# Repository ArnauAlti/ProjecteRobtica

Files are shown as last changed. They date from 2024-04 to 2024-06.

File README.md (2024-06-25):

# MiniGolfer
MiniGolfer es un robot el cual es capaz de jugar a minigolf.
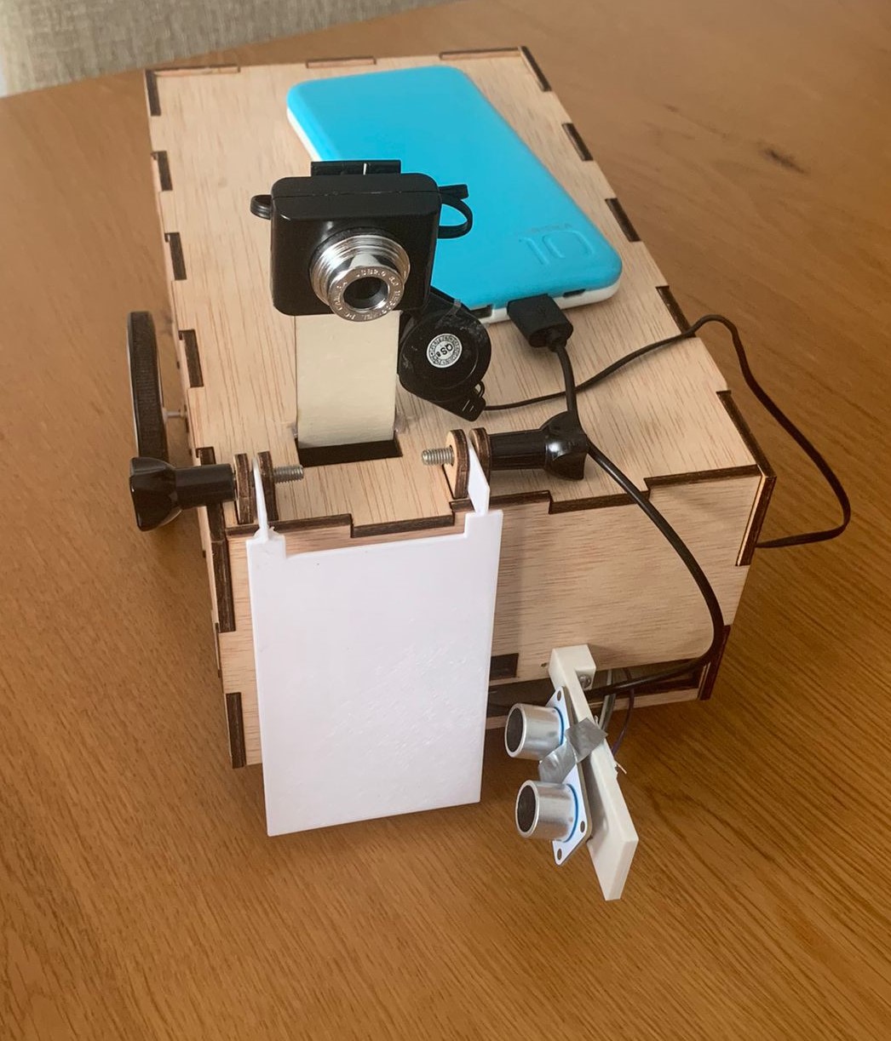
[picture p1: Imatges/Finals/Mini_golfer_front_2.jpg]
Mini_golfer


### [Contingut](#contingut)
### [Requeriments](#requeriments)
### [Components](#components)
### [Esquema HW](#esquema-hw)
### [Esquema SW](#esquema-sw)
### [Resultats Finals + Video](#resultats-finals--video)
### [Autors](#autors)

### Contingut

El robot està dissenyat per jugar al minigolf de manera autònoma. S’equipa amb dues rodes principals per al desplaçament i una roda addicional multidireccional per a una millor maniobrabilitat. El robot utilitza una càmera per localitzar i seguir la pilota de golf al camp de joc. Una vegada ha identificat la pilota, el robot s'aproxima a ella.
Per determinar la proximitat exacta a la pilota, el robot està equipat amb un sensor d'ultrasons. Quan el sensor detecta que la pilota està a l'abast, el robot s’atura. A continuació, activa un solenoide que mou una pala mecànica. Aquesta pala és responsable de colpejar la pilota, dirigir-la cap al forat.

### Requeriments
Les llibreries necessàries per aquest projecte son:
- RPi.GPIO
- OpenCV
- Numpy
- time

### Components
- Raspberry Pi 3 B+
- Cámara Raspberry
- 2 Motor Rodes
- Sensor de distancia por ultrasonidos
- Placa de prototipo
- Base para baterías (6xAA)
- Solenoide 5v
- Controlador de motores
- Bateria externa
- Relé

### Esquema HW
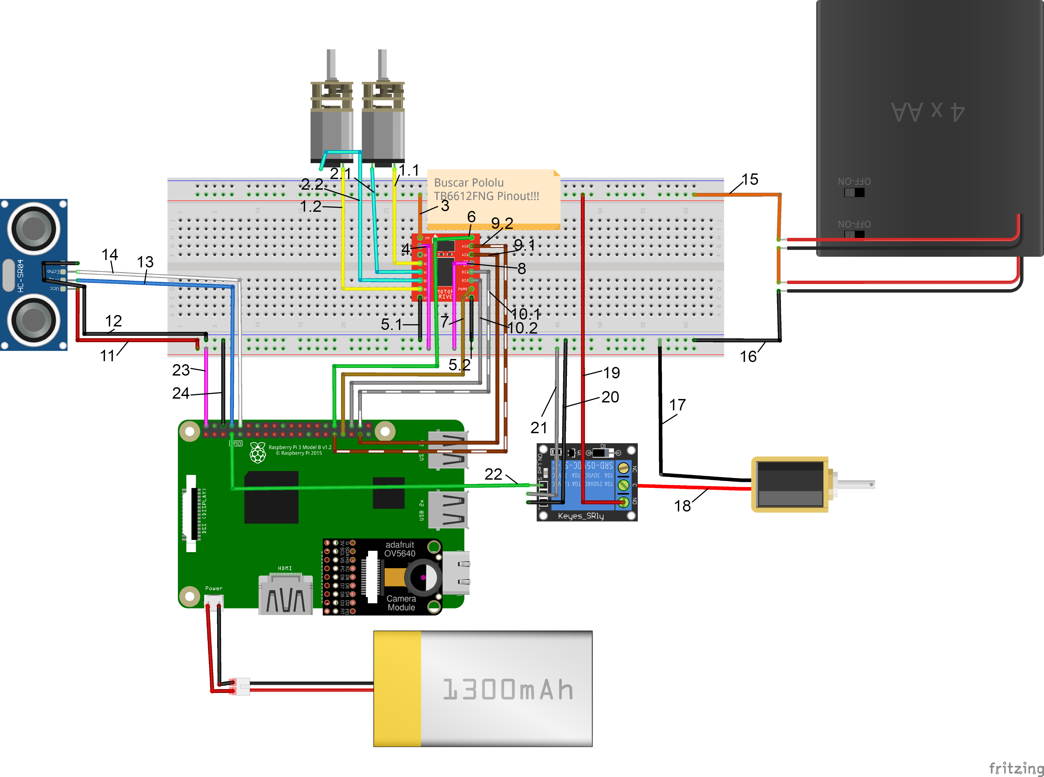
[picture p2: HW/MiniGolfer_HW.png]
MiniGolfer Hardware Diagram


1.1. Connexió positiu del motor A  
1.2. Connexió positiu del motor B  
2.1. Connexió negatiu del motor A  
2.2. Connexió negatiu del motor B  
3. Alimentació 9v  
4. 5V de Raspberry  
5.1. Connexió de terra del driver connectat al GND de Raspberry  
5.2. Connexió de terra del driver connectat al GND de Raspberry  
6. Senyal anàloga para el motor A connectat al GPIO 12 de Raspberry  
7. Senyal anàloga para el motor B connectat al GPIO 13 de Raspberry  
8. 5V de Raspberry  
9.1. Senyal d'entrada del motor A connectat al GPIO 26 de Raspberry  
9.2. Senyal d'entrada del motor A connectat al GPIO 6 de Raspberry  
10.1. Senyal d'entrada del motor B connectat al GPIO 20 de Raspberry  
10.2. Senyal d'entrada del motor B connectat al GPIO 16 de Raspberry  
11. Alimentació del sensor d'ultrasònics connectat al 5V de Raspberry  
12. Connexió de terra del sensor d'ultrasons connectat al GND de Raspberry  
13. Senyal trigger del sensor d'ultrasons connectat al GPIO 14 de Raspberry  
14. Senyal eco del sensor d'ultrasons connectat al GPIO 15 de Raspberry  
15. Positiu de la bateria  
16. GND de la bateria  
17. GND del solenoide  
18. Alimentació del solenoide  
19. Connexió alimentació del solenoide via relé  
20. GND del solenoide connectat de Raspberry  
21. VCC del Relé connectat de Raspberry  
22. Connexió de senyal de relé al GPIO 4 de Raspberry  
23. 5V de Raspberry al protoboard  
24. Connexió GND de Raspberry al protoboard  

Conexió extra USB: Càmera

### Esquema SW
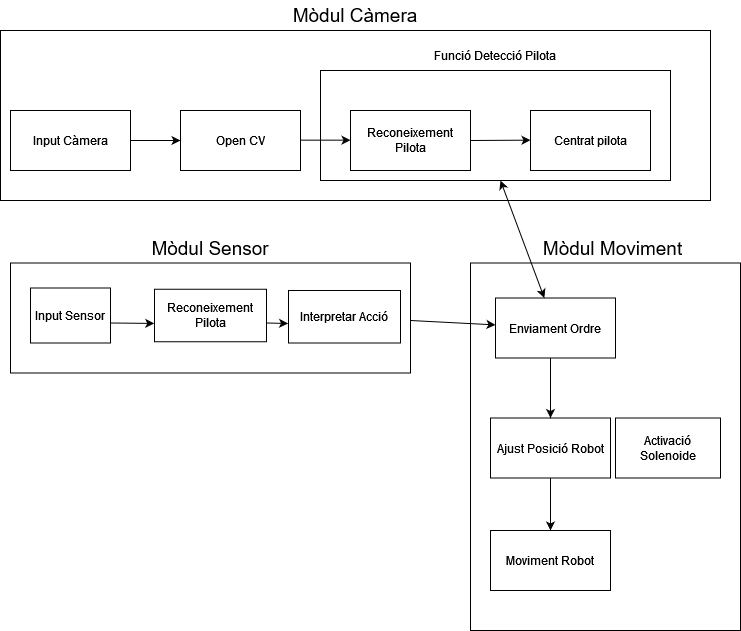
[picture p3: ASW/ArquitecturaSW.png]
Architecture MINIGOLFER


### Resultats Finals + Video
Miniatura del video (https://www.youtube.com/watch?v=eHLhcOQ6SlU)

### Autors

- Arnau Altimira Rubio
- Bernat Brustenga Garriga
- Wenpeng Ji
- Joaquim Calavera Madaula

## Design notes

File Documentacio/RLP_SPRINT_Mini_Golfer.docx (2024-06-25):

MiniGolfer

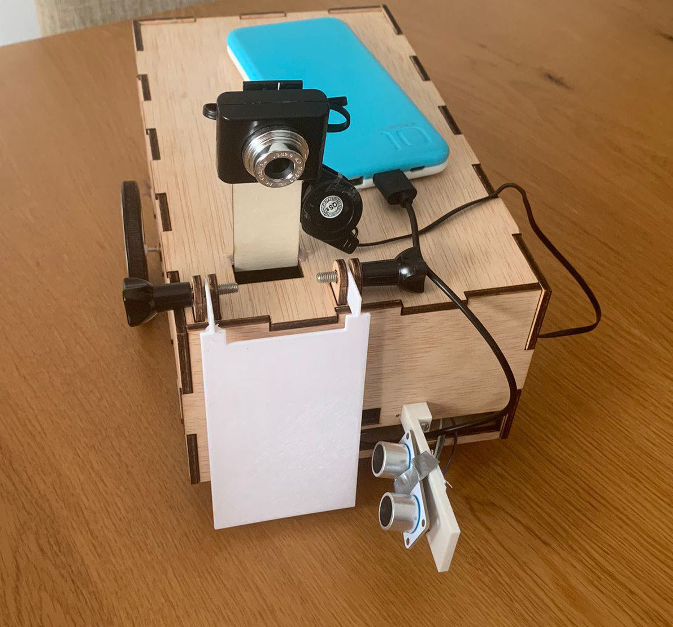
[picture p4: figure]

Arnau Altimira Rubio

Bernat Brustenga Garriga

Wenpeng Ji

Joaquim Calavera Madaula

Table of Contents

Project description 1

Electronic components 1

Scheme 2

Extra components and 3D pieces 4

Foreseen risks and contingency plan 6

MiniGolfer

Robot capaç de jugar al minigolf de forma autonoma

# Project description

El robot està dissenyat per jugar al minigolf de manera autònoma. S’equipa amb dues rodes principals per al desplaçament i una roda addicional multidireccional per a una millor maniobrabilitat. El robot utilitza una càmera per localitzar i seguir la pilota de golf al camp de joc. Una vegada ha identificat la pilota, el robot s'aproxima a ella cuidadosament.

Per determinar la proximitat exacta a la pilota, el robot està equipat amb un sensor d'ultrasons. Quan el sensor detecta que la pilota està a l'abast adequat, el robot s’atura. A continuació, activa un solenoide que mou una pala mecànica. Aquesta pala és responsable de colpejar la pilota, dirigir-la cap al forat.

# Electronic components

This is the list of the used components:

- Raspberry Pi 3 B+
- Càmera Raspberry
- Motor Rodes
- Sensor de distancia por ultrasons
- Placa de prototip
- Base para baterías (6xAA)
- Solenoide 5v
- Controlador de motors
- Bateria externa
- Relé

# Scheme

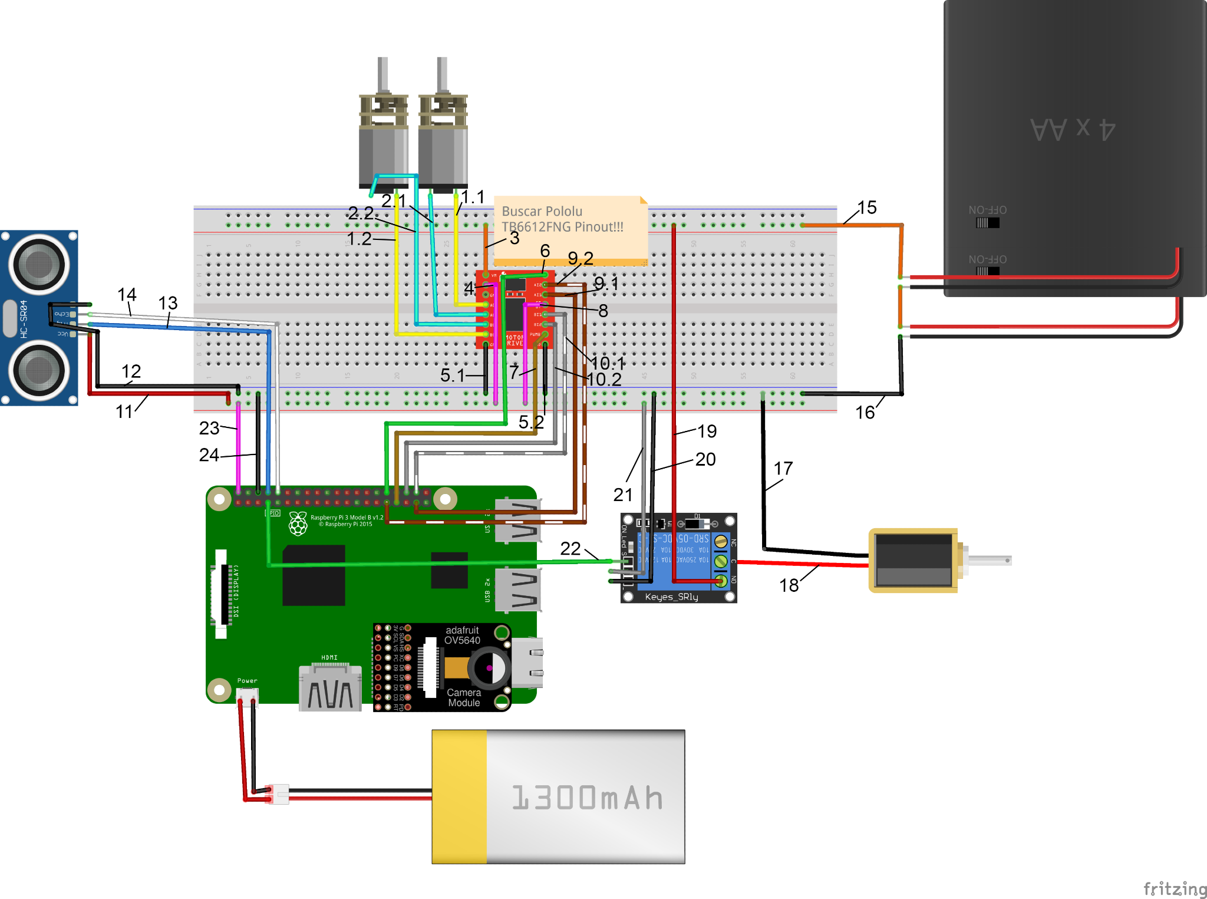
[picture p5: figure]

1.1. Connexió positiu del motor A

1.2. Connexió positiu del motor B

2.1. Connexió negatiu del motor A

2.2. Connexió negatiu del motor B

3. Alimentació 9v

4. 5V de Raspberry

5.1. Connexió de terra del driver connectat al GND de Raspberry

5.2. Connexió de terra del driver connectat al GND de Raspberry

6. Senyal anàloga para el motor A connectat al GPIO 12 de Raspberry

7. Senyal anàloga para el motor B connectat al GPIO 13 de Raspberry

8. 5V de Raspberry

9.1. Senyal d'entrada del motor A connectat al GPIO 26 de Raspberry

9.2. Senyal d'entrada del motor A connectat al GPIO 6 de Raspberry

10.1. Senyal d'entrada del motor B connectat al GPIO 20 de Raspberry

10.2. Senyal d'entrada del motor B connectat al GPIO 16 de Raspberry

11. Alimentació del sensor d'ultrasònics connectat al 5V de Raspberry

12. Connexió de terra del sensor d'ultrasons connectat al GND de Raspberry

13. Senyal trigger del sensor d'ultrasons connectat al GPIO 14 de Raspberry

14. Senyal eco del sensor d'ultrasons connectat al GPIO 15 de Raspberry

15. Positiu de la bateria

16. GND de la bateria

17. GND del solenoide

18. Alimentació del solenoide

19. Connexió alimentació del solenoide via relé

20. GND del solenoide connectat de Raspberry

21. VCC del Relé connectat de Raspberry

22. Connexió de senyal de relé al GPIO 4 de Raspberry

23. 5V de Raspberry al protoboard

24. Connexió GND de Raspberry al protoboard

Conexió extra USB: Càmera

Extra components and 3D pieces

- Caixa pel robot
- Suport per la càmera
- Fixador pel solenoide
- Paret per aguantar sensor de ultrasònics
- Suports per la pala x4
- Pala
- Caragol pala

Caixa pel robot: Caixa feta amb tall làser amb tapa extraïble, amb forats per fer les connexions amb la raspberry i per connectar les rodes, amb un forat extra per posar la molla del solenoide i empènyer la pala.

Suport per la càmera: Rectangle fet amb tall làser enganxat a la tapa de la caixa per deixar la càmera més elevada.

Fixador pel solenoide: Suport que aguanta el solenoide dins de la caixa perquè quan empenyi la pala no es mogui.

Paret per aguantar sensor d'ultrasònics: Enganxat davant del robot per col·locar un sensor d'ultrasònics apuntant davant de la pilota, aquest serveix perquè el robot pugui parar en el punt exacte perquè la pala estigui davant de la pilota.

Suports per la pala: Quatre suports enganxats a la tapa per posar la tapa mòbil.

Pala: Estructura que empenyerà el solenoide i donarà el cop a la pilota.

Caragol: Caragols per connectar la pala amb els suports de la pala per aconseguir el suport mòbil.

Fixador pel solenoide:

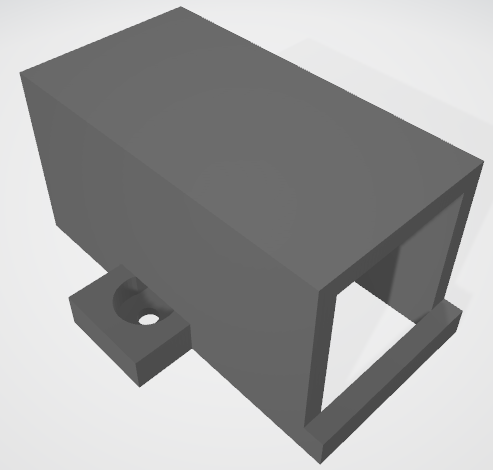
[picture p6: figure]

Paret per aguantar sensor de ultrasonidos:

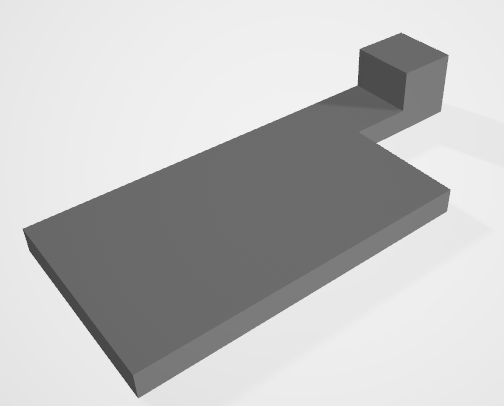
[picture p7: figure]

Suports per la pala x4:

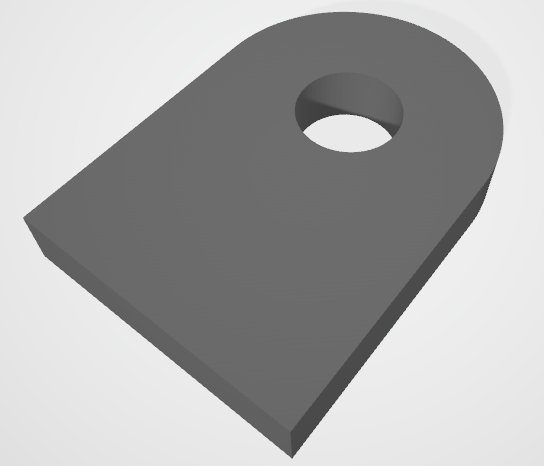
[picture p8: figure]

Pala:

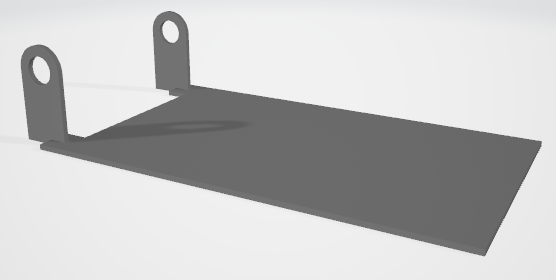
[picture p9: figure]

Caragol pala:

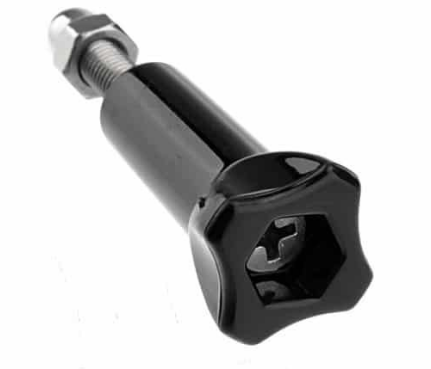
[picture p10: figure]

Risk # | Description | Probability (High/Medium/Low) | Impact (High/Medium/Low) | Contingency plan
Potència solenoide | El solenoide pot no tenir la suficient potència per empènyer la pilota a una certa distància. | Medium | Medium | Girar el solenoide, ja que hem trobat que té més potència quan comprimeix la molla que en l'etapa posterior.
Detecció càmera | No hi ha suficient camp de visió amb la càmera del projecte per trobar la pilota. | Medium | Low | No fa falta que la imatge de la càmera tingui la pilota en la imatge, el robot es pot moure fins a trobar la pilota.
Potencia motors de la roda | No tenir la suficient potencia per moure el robot | Low | High | Canviar a motors més potents o treure pes al robot.

References

This project has been inspired by the following Internet projects:

https://developer.nvidia.com/blog/jetson-project-of-the-month-this-autonomous-soccer-robot-can-point-shoot-and-score/

https://www.youtube.com/watch?v=jYL_Gjumi4I (Construir Robot Minigolf lego)

RPL - Computer Engineering. UAB (Barcelona) 2023-2024

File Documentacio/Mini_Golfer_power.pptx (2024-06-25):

## MiniGolfer


Un robot capaç de jugar al minigolf de forma autónoma

Arnau Altimira Rubio
Bernat Brustenga Garriga
Wenpeng Ji
Joaquim Calavera Madaula

ROBÒTICA, LLENGUATGE I PLANIFICACIÓ – ENGINYERIA INFORMÀTICA - UAB

## 1.Arquitectura hardware

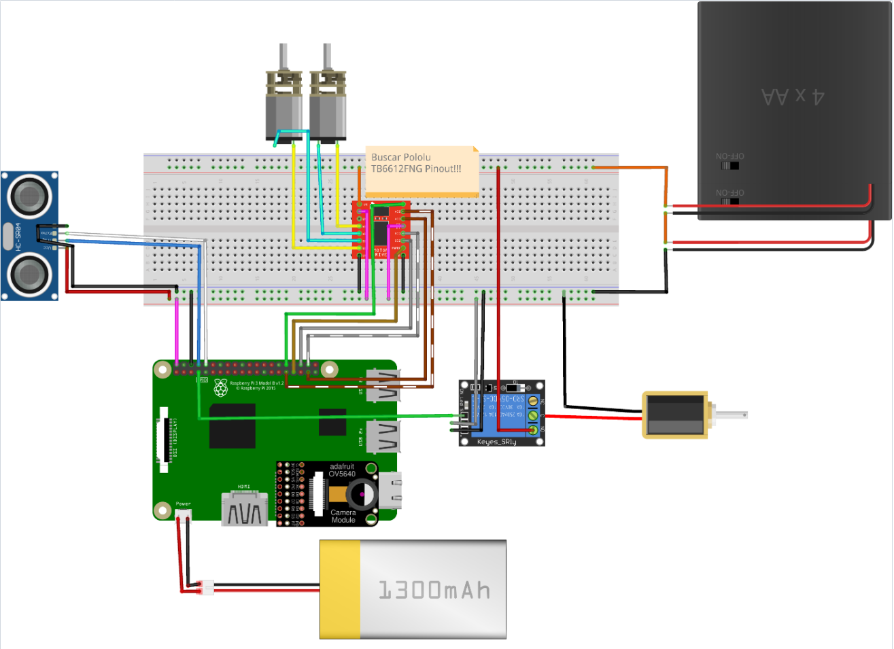
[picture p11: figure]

## 2.Arquitectura software


## 3. Algorísmica

- 1-Moviment rotatori -> Buscar Pilota
- 2-Pilota trobada -> Centrar la pilota amb la pala
- 3-Aproximació a la pilota -> sensor detecta pilota prop de la pala
- 4-Activació del solenoide per a golpejar la pilota

## Fotos, Video i Git

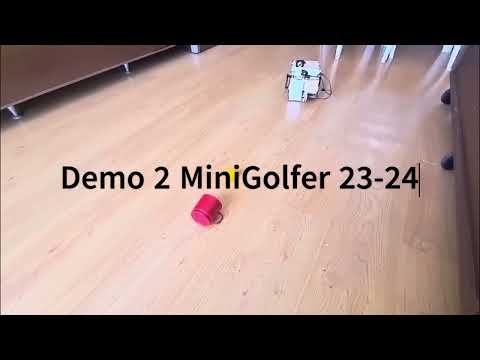
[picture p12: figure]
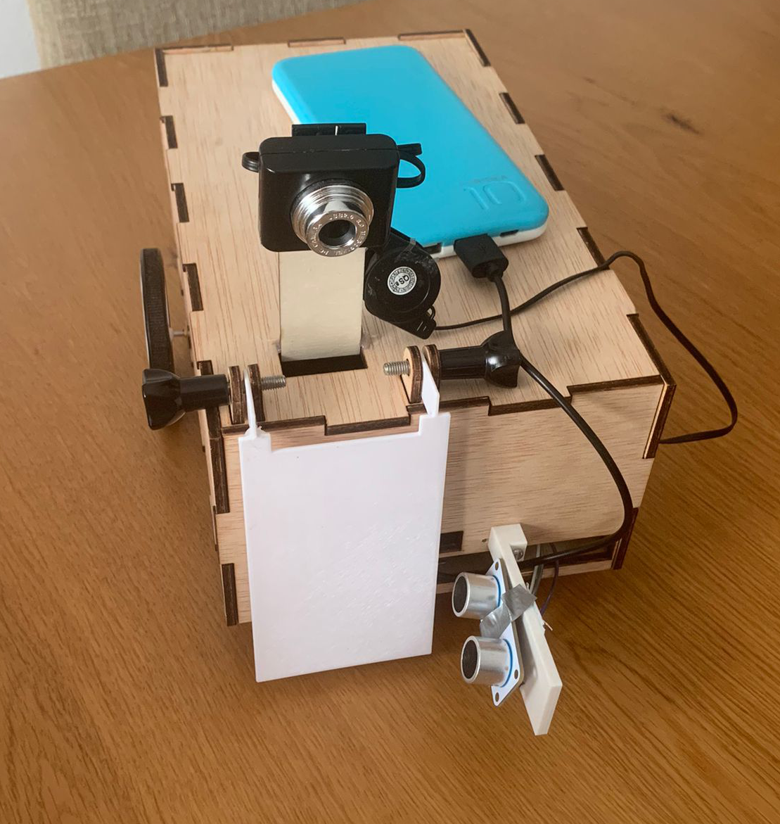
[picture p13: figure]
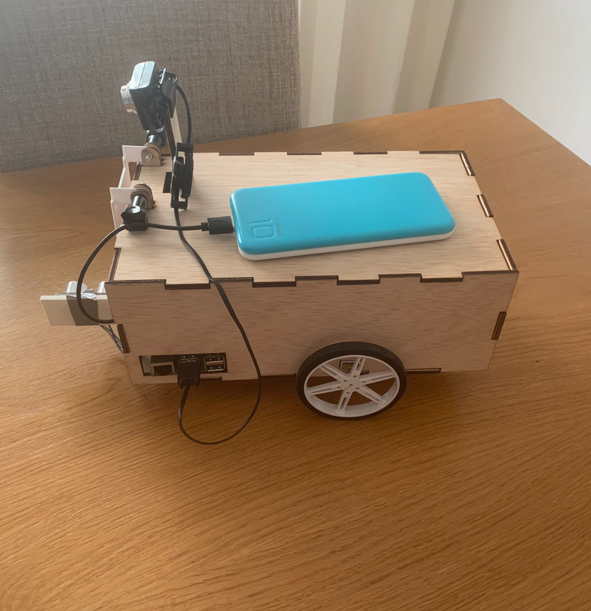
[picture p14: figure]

https://github.com/ArnauAlti/ProjecteRobtica/tree/main

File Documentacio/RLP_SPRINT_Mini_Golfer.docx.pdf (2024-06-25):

RPL - Computer Engineering. UAB (Barcelona) 2023-2024

# MiniGolfer

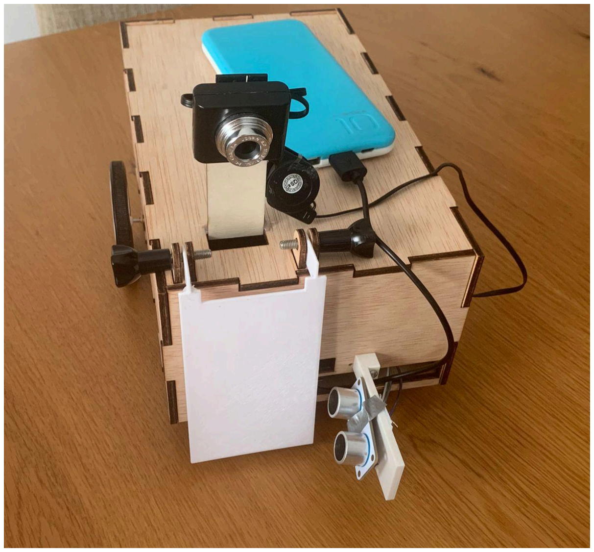
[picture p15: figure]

Arnau Altimira Rubio

Bernat Brustenga Garriga

Wenpeng Ji

Joaquim Calavera Madaula

# Table of Contents

ROBOT_NAME

# MiniGolfer

Robot capaç de jugar al minigolf de forma autonoma

Project description

El robot està dissenyat per jugar al minigolf de manera autònoma. S’equipa amb dues rodes principals per al desplaçament i una roda addicional multidireccional per a una millor maniobrabilitat. El robot utilitza una càmera per localitzar i seguir la pilota de golf al camp de joc. Una vegada ha identificat la pilota, el robot s'aproxima a ella cuidadosament.

Per determinar la proximitat exacta a la pilota, el robot està equipat amb un sensor d'ultrasons. Quan el sensor detecta que la pilota està a l'abast adequat, el robot s’atura. A continuació, activa un solenoide que mou una pala mecànica. Aquesta pala és responsable de colpejar la pilota, dirigir-la cap al forat.

Electronic components
This is the list of the used components:

■ Raspberry Pi 3 B+
■ Càmera Raspberry
■ Motor Rodes
■ Sensor de distancia por ultrasons ■ Placa de prototip
■ Base para baterías (6xAA)
■ Solenoide 5v
■ Controlador de motors
■ Bateria externa
■ Relé
ROBOT_NAME | 1

Scheme

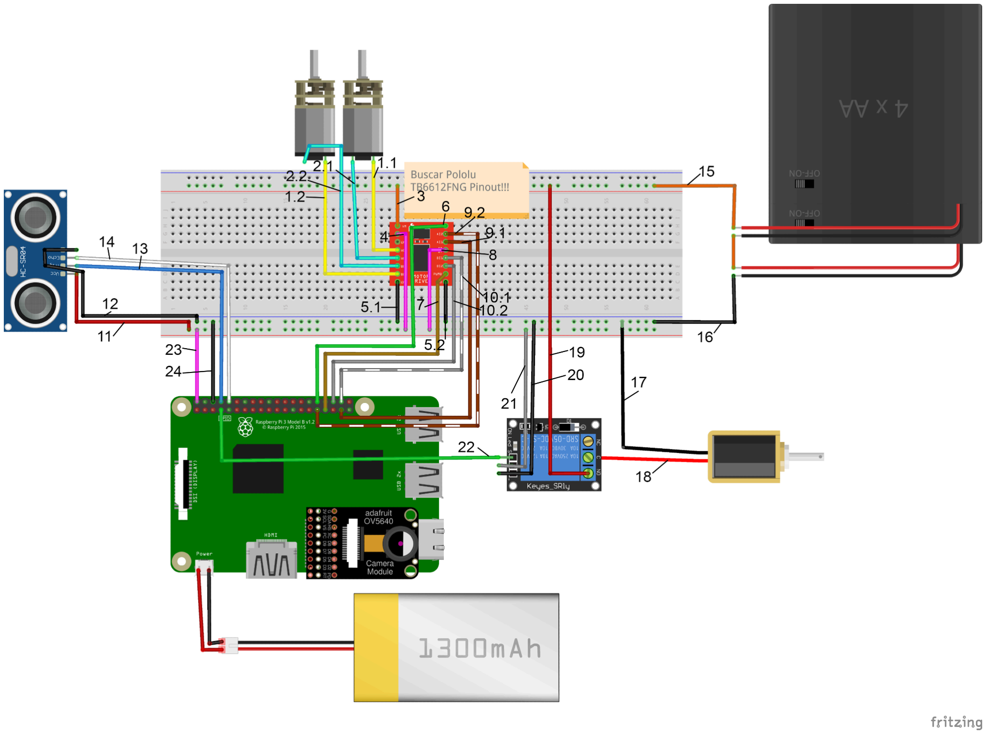
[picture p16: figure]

MiniGolfer | 2

### 1.1. Connexió positiu del motor A 1.2. Connexió positiu del motor B 2.1. Connexió negatiu del motor A 2.2. Connexió negatiu del motor B 3. Alimentació 9v

4. 5V de Raspberry

### 5.1. Connexió de terra del driver connectat al GND de Raspberry 5.2. Connexió de terra del driver connectat al GND de Raspberry 6. Senyal anàloga para el motor A connectat al GPIO 12 de Raspberry 7. Senyal anàloga para el motor B connectat al GPIO 13 de Raspberry

8. 5V de Raspberry

9.1. Senyal d'entrada del motor A connectat al GPIO 26 de Raspberry 9.2. Senyal d'entrada del motor A connectat al GPIO 6 de Raspberry 10.1. Senyal d'entrada del motor B connectat al GPIO 20 de Raspberry 10.2. Senyal d'entrada del motor B connectat al GPIO 16 de Raspberry 11. Alimentació del sensor d'ultrasònics connectat al 5V de Raspberry 12. Connexió de terra del sensor d'ultrasons connectat al GND de Raspberry 13. Senyal trigger del sensor d'ultrasons connectat al GPIO 14 de Raspberry 14. Senyal eco del sensor d'ultrasons connectat al GPIO 15 de Raspberry 15. Positiu de la bateria 16. GND de la bateria 17. GND del solenoide 18. Alimentació del solenoide 19. Connexió alimentació del solenoide via relé 20. GND del solenoide connectat de Raspberry 21. VCC del Relé connectat de Raspberry 22. Connexió de senyal de relé al GPIO 4 de Raspberry
23. 5V de Raspberry al protoboard

### 24. Connexió GND de Raspberry al protoboard

Conexió extra USB: Càmera

MiniGolfer | 3

Extra components and 3D pieces

■ Caixa pel robot

■ Suport per la càmera

■ Fixador pel solenoide

■ Paret per aguantar sensor de ultrasònics

■ Suports per la pala x4

■ Pala

■ Caragol pala

Caixa pel robot: Caixa feta amb tall làser amb tapa extraïble, amb forats per fer les connexions amb la raspberry i per connectar les rodes, amb un forat extra per posar la molla del solenoide i empènyer la pala.

Suport per la càmera: Rectangle fet amb tall làser enganxat a la tapa de la caixa per deixar la càmera més elevada.

Fixador pel solenoide: Suport que aguanta el solenoide dins de la caixa perquè quan empenyi la pala no es mogui.

Paret per aguantar sensor d'ultrasònics: Enganxat davant del robot per col·locar un sensor d'ultrasònics apuntant davant de la pilota, aquest serveix perquè el robot pugui parar en el punt exacte perquè la pala estigui davant de la pilota.

Suports per la pala: Quatre suports enganxats a la tapa per posar la tapa mòbil.

Pala: Estructura que empenyerà el solenoide i donarà el cop a la pilota.

Caragol: Caragols per connectar la pala amb els suports de la pala per aconseguir el suport mòbil.

MiniGolfer | 4

Fixador pel solenoide:

Paret per aguantar sensor de ultrasonidos:

Suports per la pala x4:

Pala:


Caragol pala:

MiniGolfer | 5

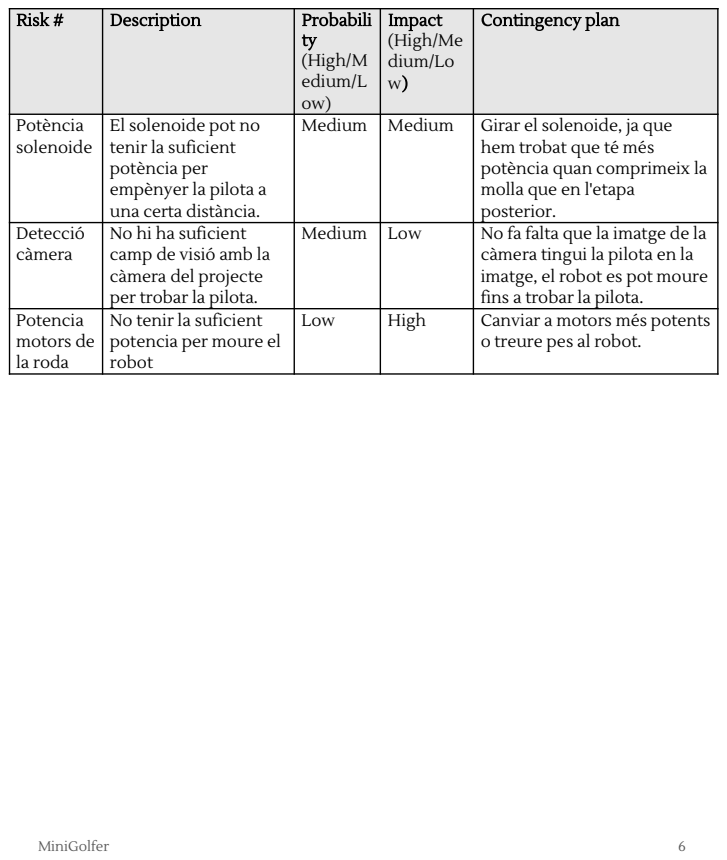
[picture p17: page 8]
MiniGolfer

Risk # | Description | Probabili ty (High/M edium/L ow) | Impact (High/Me dium/Lo w) | Contingency plan

Potència solenoide | El solenoide pot no tenir la suficient potència per empènyer la pilota a una certa distància. | Medium | Medium | Girar el solenoide, ja que hem trobat que té més potència quan comprimeix la molla que en l'etapa posterior.

Detecció càmera | No hi ha suficient camp de visió amb la càmera del projecte per trobar la pilota. | Medium | Low | No fa falta que la imatge de la càmera tingui la pilota en la imatge, el robot es pot moure fins a trobar la pilota.

Potencia motors de la roda | No tenir la suficient potencia per moure el robot | Low | High | Canviar a motors més potents o treure pes al robot.

# References

This project has been inspired by the following Internet projects:

https://developer.nvidia.com/blog/jetson-project-of-the-month-this-autonomous-soccer-robot-can-point-shoot-and-score/

https://www.youtube.com/watch?v=jYL_Gjumi4I (Construir Robot Minigolf lego)

MiniGolfer | 7

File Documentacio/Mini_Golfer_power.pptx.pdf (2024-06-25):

# MiniGolfer

Arnau Altimira Rubio

Bernat Brustenga Garriga

Wenpeng Ji

Joaquim Calavera Madaula

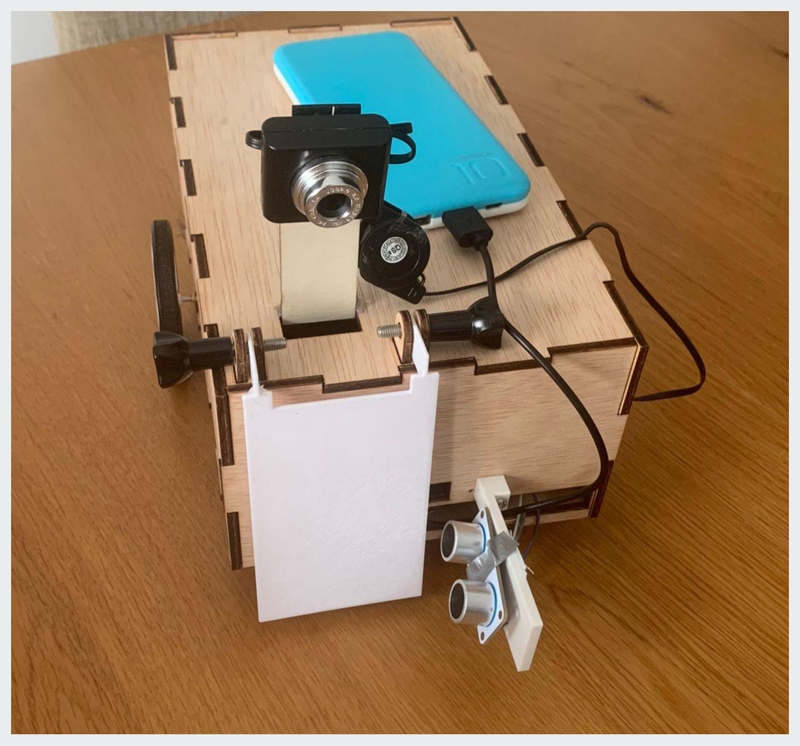
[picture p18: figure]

Un robot capaç de jugar al minigolf de forma autónoma

ROBÒTICA, LLENGUATGE I PLANIFICACIÓ – ENGINYERIA INFORMÀTICA - UAB

# 1.Arquitectura hardware

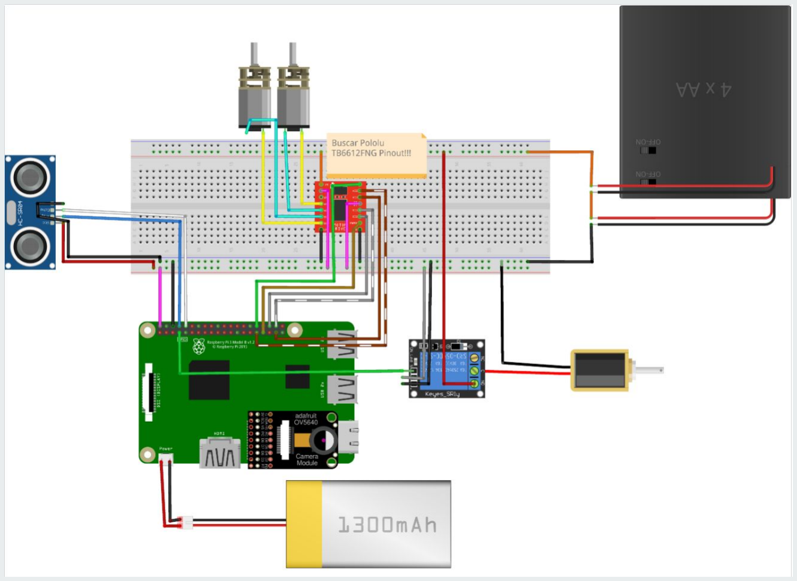
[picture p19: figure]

# 2.Arquitectura software

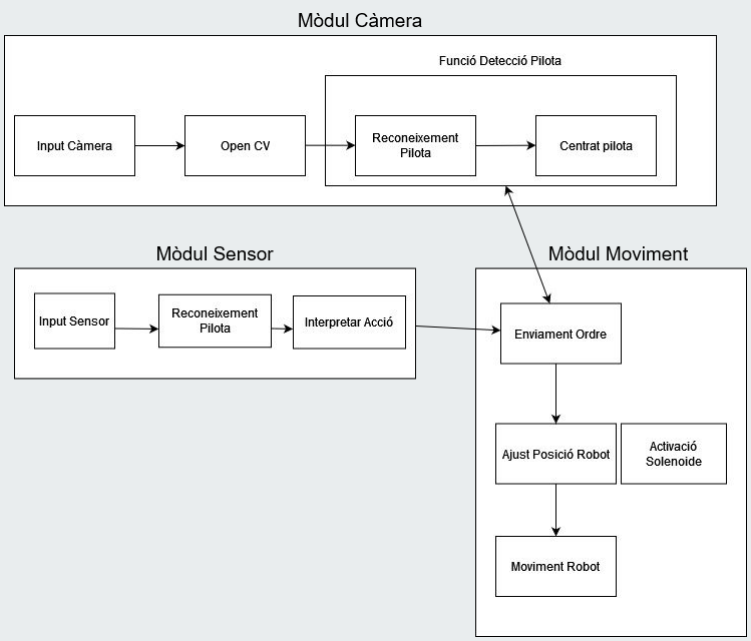
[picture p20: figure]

# 3. Algorísmica

1-Moviment rotatori -> Buscar Pilota

2-Pilota trobada -> Centrar la pilota amb la pala

3-Aproximació a la pilota -> sensor detecta pilota prop de la pala

4-Activació del solenoide per a golpejar la pilota

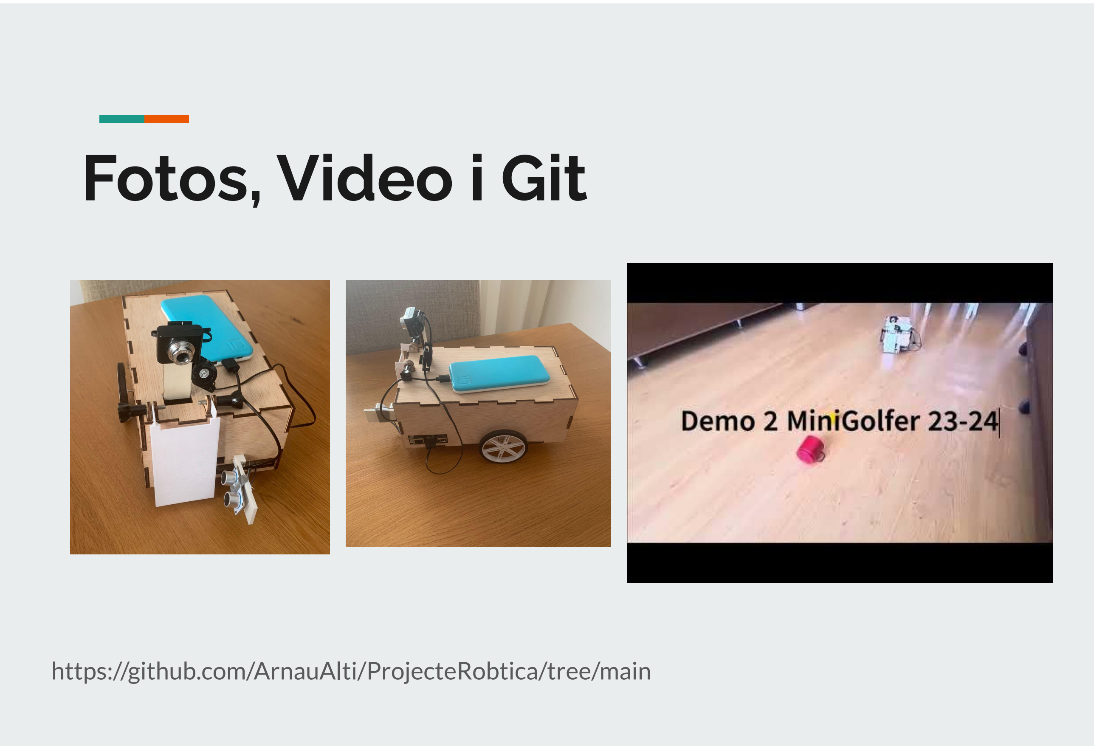
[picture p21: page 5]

# Fotos, Video i Git

https://github.com/ArnauAlti/ProjecteRobtica/tree/main

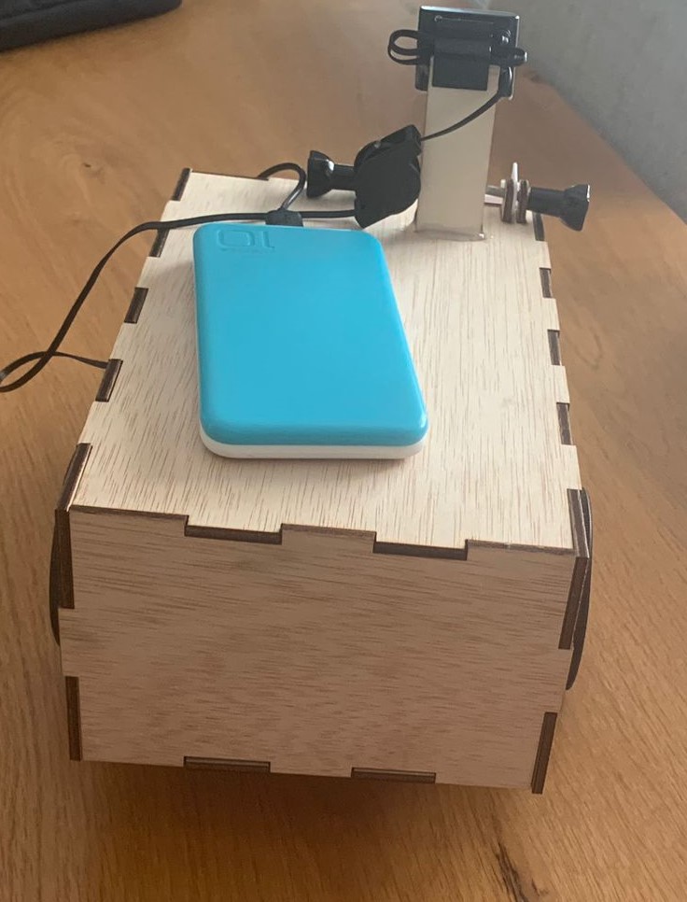
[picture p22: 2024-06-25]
Imatges/Finals/Mini_golfer_back.jpg

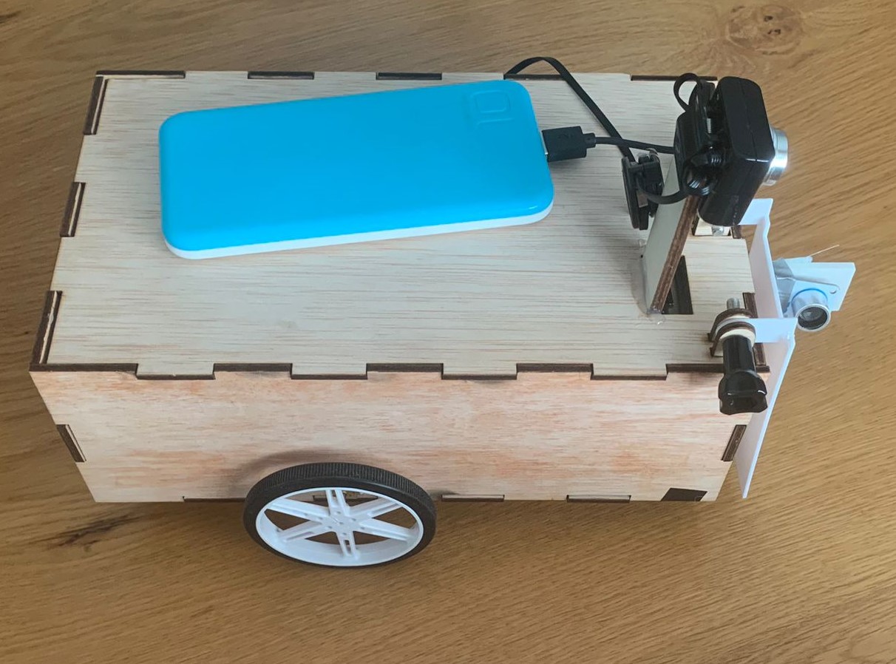
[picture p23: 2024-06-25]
Imatges/Finals/Mini_golfer_left.jpg

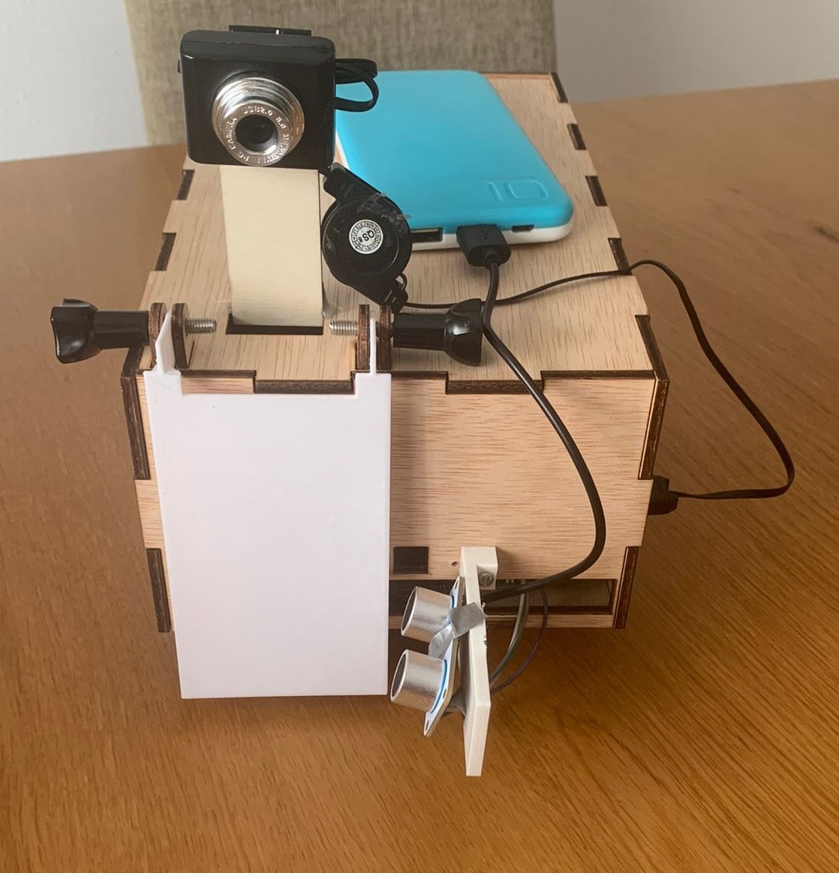
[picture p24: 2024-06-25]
Imatges/Finals/Mini_golfer_front.jpg

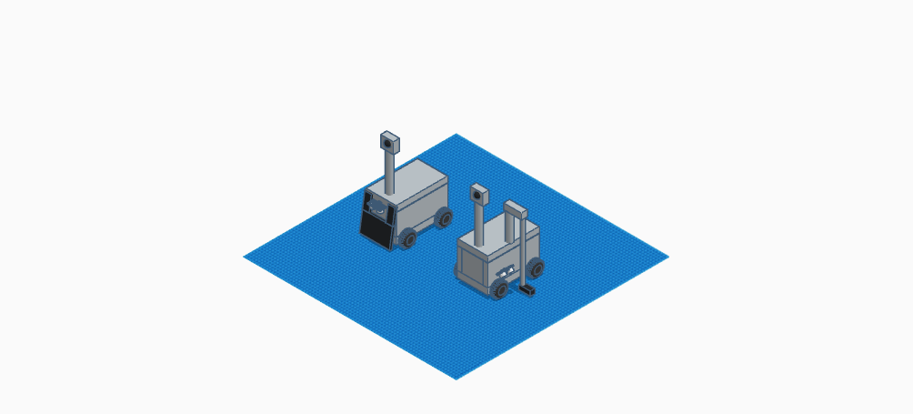
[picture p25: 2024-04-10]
Imatges/Previes/Minigolf_Model_1.png

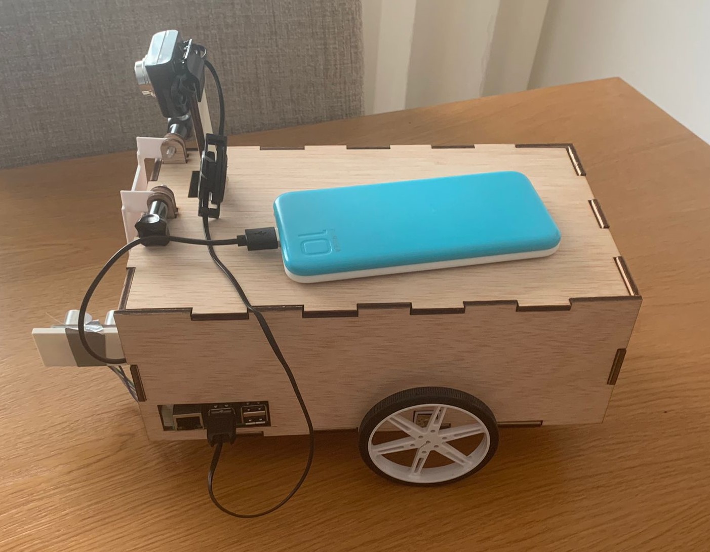
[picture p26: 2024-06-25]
Imatges/Finals/Mini_golfer_right.jpg

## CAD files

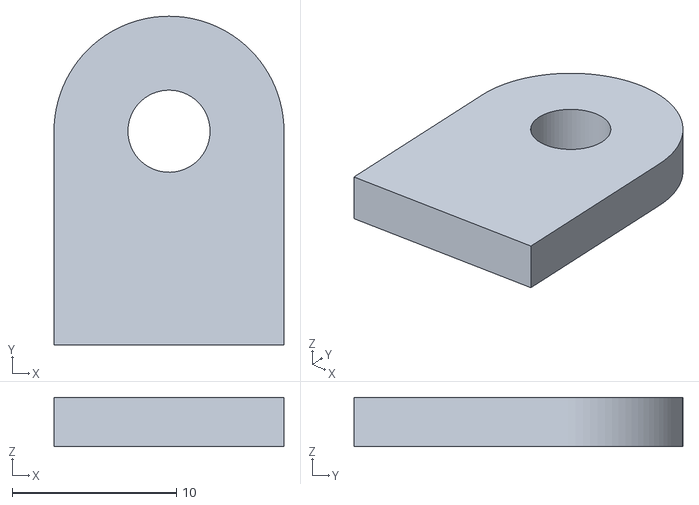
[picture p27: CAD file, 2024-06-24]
Models/Soport pala.stl
14.0 x 20.0 x 3.00

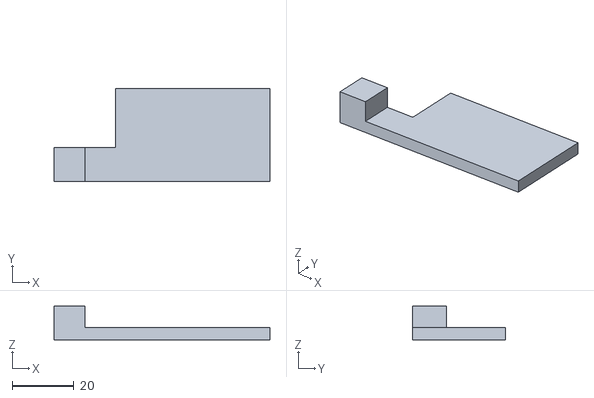
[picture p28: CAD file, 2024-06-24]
Models/Ultrasonidos.stl
70.0 x 30.0 x 11.0

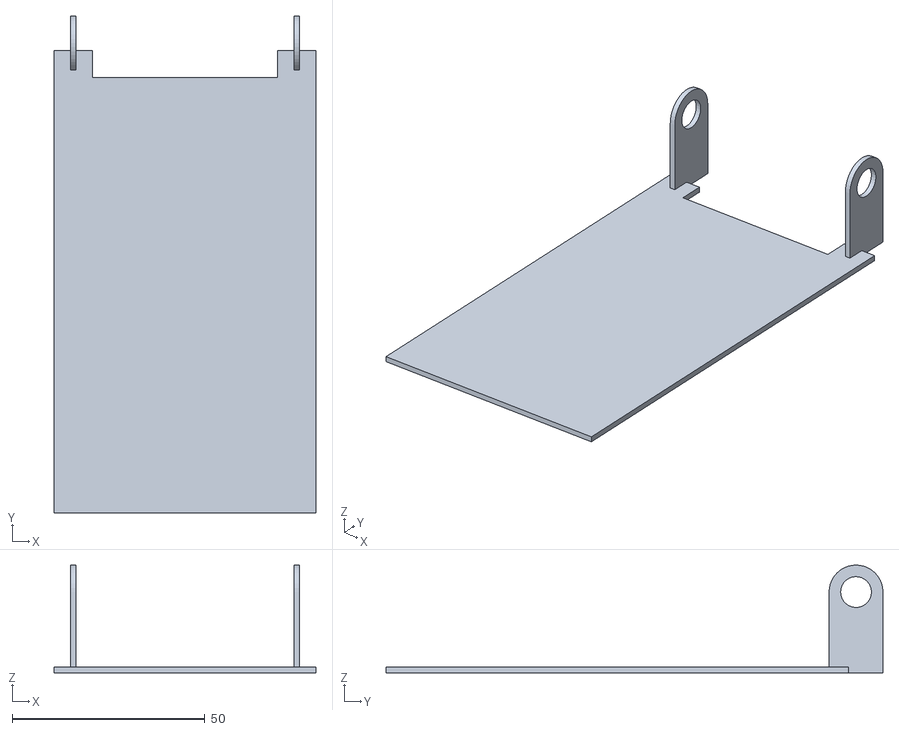
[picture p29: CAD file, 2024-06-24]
Models/PalaFinal.stl
68.0 x 129.0 x 28.0

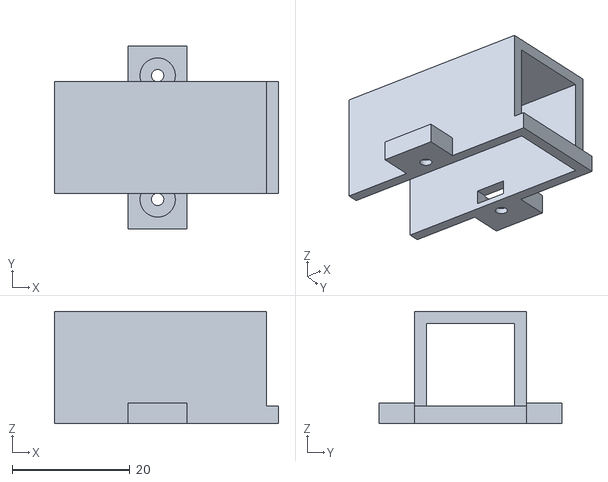
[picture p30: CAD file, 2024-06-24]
Models/Solenoide.stl
38.0 x 31.0 x 19.0

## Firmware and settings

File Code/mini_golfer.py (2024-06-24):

import cv2 as cv
import numpy as np
import RPi.GPIO as GPIO
import time

PWMA = 12
PWMB = 13
BIN1 = 20
BIN2 = 16
AIN1 = 26
AIN2 = 6
solenoid_pin = 4
GPIO_TRIGGER = 15 
GPIO_ECHO = 14

GPIO.setmode(GPIO.BCM)
GPIO.setup(PWMA, GPIO.OUT)
GPIO.setup(PWMB, GPIO.OUT)
GPIO.setup(AIN1, GPIO.OUT)
GPIO.setup(AIN2, GPIO.OUT)
GPIO.setup(BIN1, GPIO.OUT)
GPIO.setup(BIN2, GPIO.OUT)
GPIO.setup(solenoid_pin, GPIO.OUT)
GPIO.setup(GPIO_TRIGGER, GPIO.OUT)
GPIO.setup(GPIO_ECHO, GPIO.IN)

pwmA = GPIO.PWM(PWMA, 1000)
pwmB = GPIO.PWM(PWMB, 1000)
pwmA.start(0)
pwmB.start(0)

def motorA_forward(speed: int):
    GPIO.output(AIN1, GPIO.HIGH)
    GPIO.output(AIN2, GPIO.LOW)
    pwmA.ChangeDutyCycle(speed)
    
def motorA_backward(speed: int):
    GPIO.output(AIN1, GPIO.LOW)
    GPIO.output(AIN2, GPIO.HIGH)
    pwmA.ChangeDutyCycle(speed)

def motorB_forward(speed: int):
    GPIO.output(BIN1, GPIO.HIGH)
    GPIO.output(BIN2, GPIO.LOW)
    pwmB.ChangeDutyCycle(speed)

def motorB_backward(speed: int):
    GPIO.output(BIN1, GPIO.LOW)
    GPIO.output(BIN2, GPIO.HIGH)
    pwmB.ChangeDutyCycle(speed)

def motor_stop():
    GPIO.output(AIN1, GPIO.LOW)
    GPIO.output(AIN2, GPIO.LOW)
    GPIO.output(BIN1, GPIO.LOW)
    GPIO.output(BIN2, GPIO.LOW)
    pwmA.ChangeDutyCycle(0)
    pwmB.ChangeDutyCycle(0)

def activate_solenoid(duration):
    GPIO.output(solenoid_pin, GPIO.HIGH)
    time.sleep(duration)
    GPIO.output(solenoid_pin, GPIO.LOW)

def measure_distance():
    GPIO.output(GPIO_TRIGGER, False)
    time.sleep(0.5)
    
    GPIO.output(GPIO_TRIGGER, True)
    time.sleep(0.00001)
    GPIO.output(GPIO_TRIGGER, False)
    
    while GPIO.input(GPIO_ECHO) == 0:
        pulse_start = time.time()
    
    while GPIO.input(GPIO_ECHO) == 1:
        pulse_end = time.time()
    
    pulse_duration = pulse_end - pulse_start
    distance = pulse_duration * 17150
    return round(distance, 2)


def find_ball(frame):
    hsv = cv.cvtColor(frame, cv.COLOR_BGR2HSV)
    lower_red = np.array([5, 150, 150])
    upper_red = np.array([20, 255, 255])
    mask = cv.inRange(hsv, lower_red, upper_red)
    contours, _ = cv.findContours(mask, cv.RETR_TREE, cv.CHAIN_APPROX_SIMPLE)
    if contours:
        largest_contour = max(contours, key=cv.contourArea)
        M = cv.moments(largest_contour)
        if M['m00'] != 0:
            cx = int(M['m10'] / M['m00'])
            cy = int(M['m01'] / M['m00'])
            cv.circle(frame, (cx, cy), 10, (0, 0, 255), -1)
            return cx, cy, cv.contourArea(largest_contour)
    return None, None, 0

def move_robot(cx, cy, area, frame_width):
    if cx is None:
        motorA_forward(60)
        motorB_backward(0)
        print("No object detected, searching...")
        return True
    
    center_x = frame_width // 2
    threshold = 100    

    if abs(cx - center_x) <= threshold:
        print("Object detected")
        distance = measure_distance()
        while distance >= 5:
            print(f"Distance: {distance} cm")
            motorA_forward(60)
            motorB_forward(60)
            distance = measure_distance()
        motor_stop()
        activate_solenoid(1)
        return False
    else:
        if cx < center_x:
            motorA_forward(30)
            motorB_backward(30)
        else:
            motorA_backward(30)
            motorB_forward(30)
        return True

cap = cv.VideoCapture(0)
time.sleep(2)

try:
    while True:
        ret, frame = cap.read()
        if not ret:
            break
        
        cx, cy, area = find_ball(frame)
        if not move_robot(cx, cy, area, frame.shape[1]):
            break
        
        cv.imshow('Frame', frame)
        if cv.waitKey(1) & 0xFF == ord('q'):
            break

except KeyboardInterrupt:
    pass

finally:
    cap.release()
    cv.destroyAllWindows()
    pwmA.stop()
    pwmB.stop()
    GPIO.cleanup()

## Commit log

2024-05-29 Update HW
    [MiniGolfer.fzz]
2024-06-24 Rename Soport pala.stl to Models/Soport pala.stl
    [Soport pala.stl]
